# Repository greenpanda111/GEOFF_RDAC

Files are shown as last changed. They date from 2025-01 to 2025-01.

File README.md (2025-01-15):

# GEOFF
 3rd Year Engineering Module

 GEOFF is a 2 wheeled skid steered maze solving robot consisting of:
 2 motors with an ecoder each
 The encoders are wired to the ARB board using the expected pins as well as spare GPIO for the ultrasonics.
 
 4 IR sensors
 Two on the front for wall alignment using triganometry to calculate the angle to turn and for a wider field of view.
 One on either side of the robot for measuring the distance to the left and right of the robot.

 2 Ultrasonic sensors
 These are not currently utilised but my CAD design allows for them to be freely rotated so could be added for improved mapping capabilities in future.
 
 4 LED NeoPixel panels
 These form a 16x16 LED matrix to display live mapping of obstacles and route travelled along with current location and heading.
 The graphics library (All three NeoPixel libraries are created by Adafruit) used can allow for easy debugging. For example: writing the current angle onto the screen to test if it is being updated correctly as the robot turns.

 The Neopixel matrix can be controlled with one 5V signal pin. To achieve this, I had to design a level shifter to control it with the arduinos 3V3 signal

 2 Microswitches attached to the front corners of the robot to create a front bumper
 These prevent the robot from crashing into obstacles that the front IRs did not detect or catching on corners

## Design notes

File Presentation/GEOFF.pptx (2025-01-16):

## GEOFF

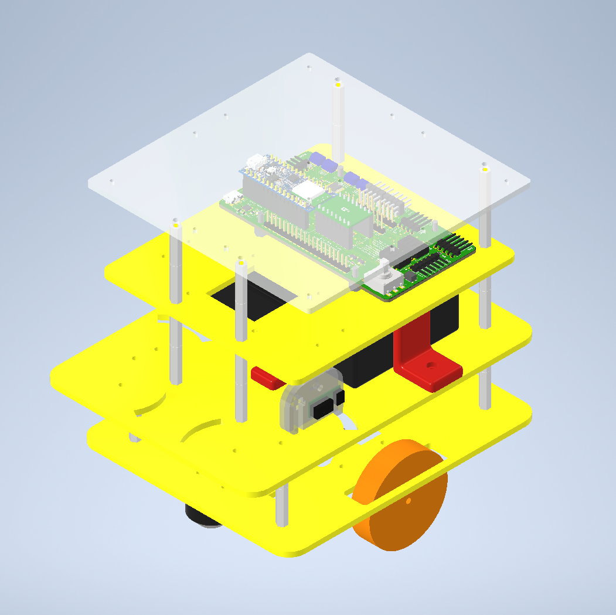
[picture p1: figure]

Ben Wiltshire

## LED Matrix

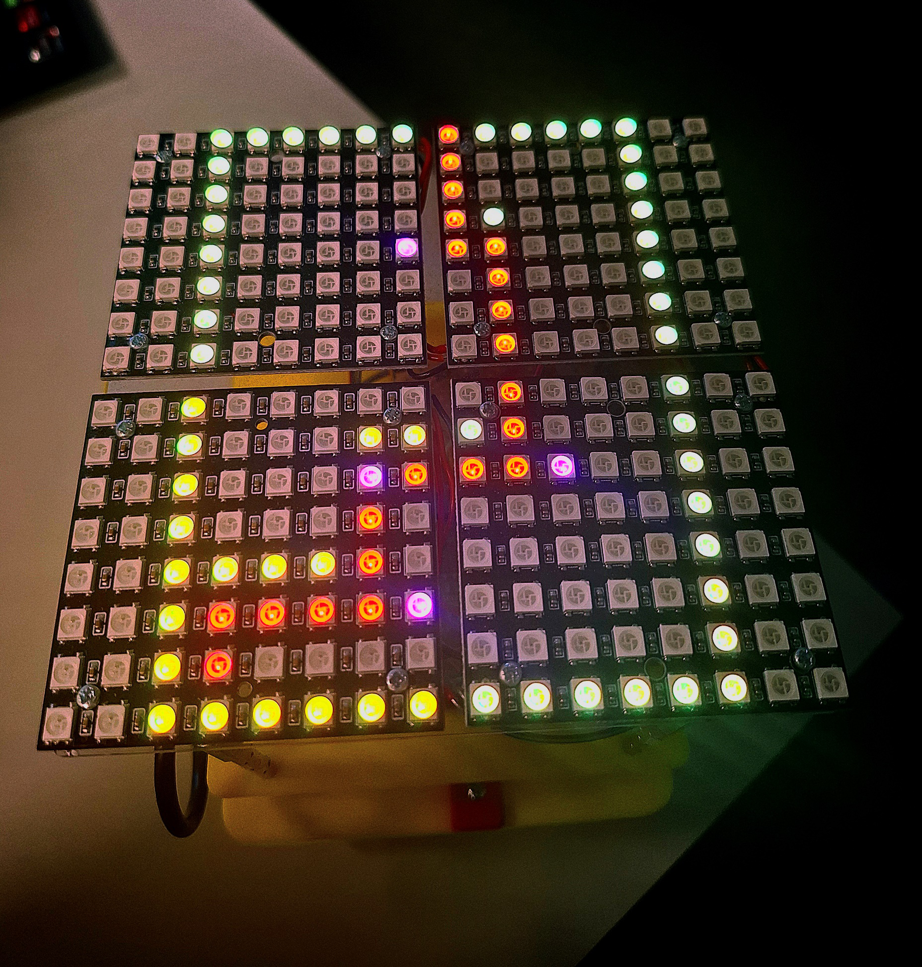
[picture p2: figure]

- 16x16 NeoPixel array
- Single pin programming
- Requires level shifter due to 5V signal
- Visualise maze solving in real time
Blue: Current Location
Red: Path Taken
Green: Obstacles
Purple: Direction

## Design

- 4 levels
- Minimum size is determined by the LED matrix
- Sensors on swivels
- Bottom IR not on swivel to keep wall aligning precise
- Cover over IR to prevent light interference
- Cable routing
- Optional slots for front ultrasonics

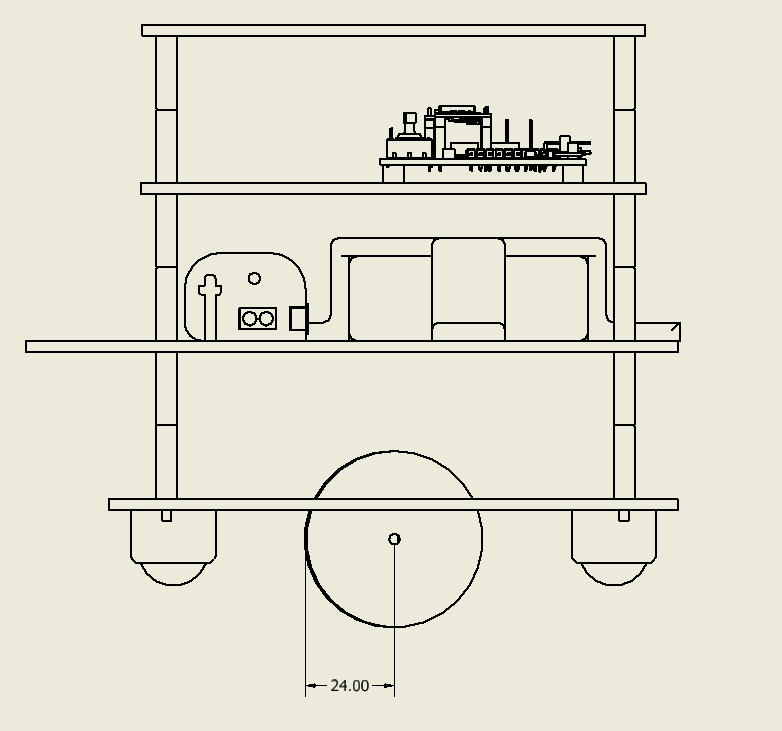
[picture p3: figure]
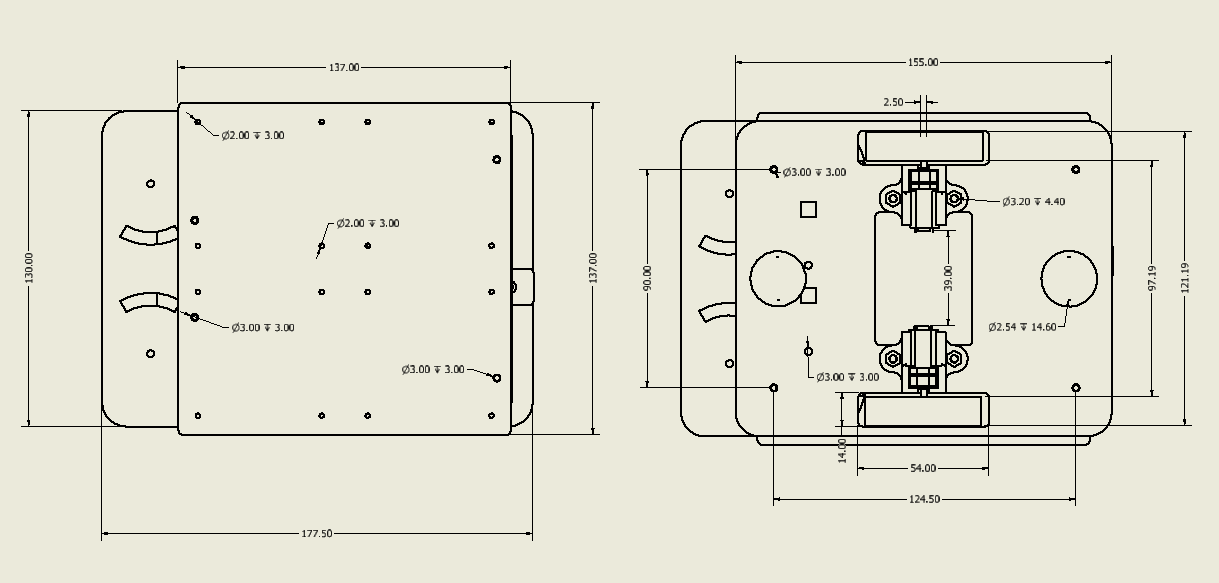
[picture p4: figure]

## Maze Solving

Turn to face the finish
Drive towards the finish until an obstacle is reached
Take measurements and take the best route around the obstacle
Shuffle along wall until it can move forward, towards the finish
If stuck in a dead end, navigate out

## Wall Aligning

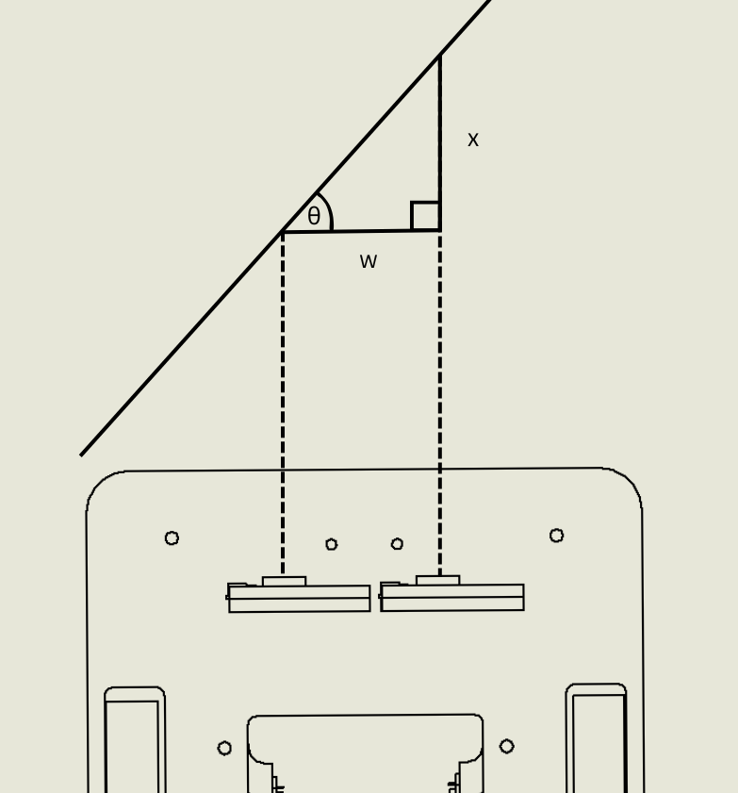
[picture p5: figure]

Trigonometry

## PCB

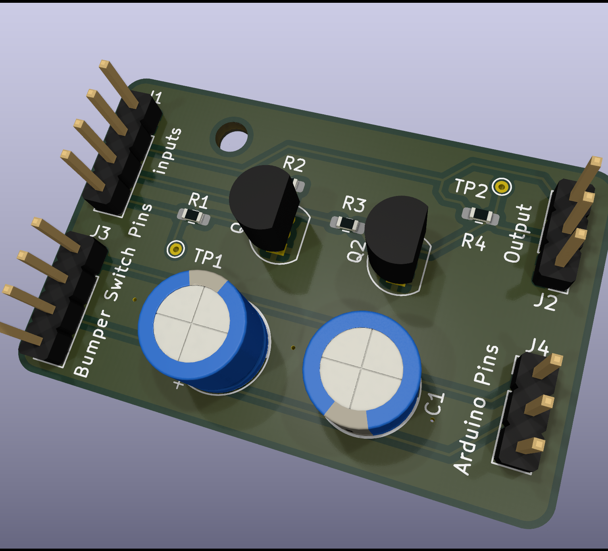
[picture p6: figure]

- LED Matrix Level Shifter
- Bumper Debouncing

## Next Steps…

Higher resolution occupancy grid
Calculating location of surrounding objects with side sensors after each move
Each bumper causing the robot to react differently

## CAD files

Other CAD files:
CAD/Final robot assembly Drawing.dwg
CAD/OldVersions/Final robot assembly Drawing.0003.dwg
CAD/0.75in Ball Caster (Pololu).ipt
CAD/Back.ipt
CAD/Battery 2023.ipt
CAD/Battery mount.ipt
CAD/Battery mount_MIR.ipt
CAD/Bottom layer.iam
CAD/Bottom layer2.ipt
CAD/Final robot assembly.iam
CAD/Front.ipt
CAD/IR Sensor Mount.iam
CAD/IR Sensor Mount.ipt
CAD/IR Sensor.ipt
CAD/M2.5 Hex Spacer 20mm 2023.ipt
CAD/M2.5 Hex Spacer 20mm.ipt
CAD/M2.5 Hex Spacer 5mm.ipt
CAD/Middle layer.iam
CAD/Middle layer.ipt
CAD/Motor assembly.iam
CAD/MotorHolder.ipt
CAD/NeoPixel Base.ipt
CAD/OldVersions/Bottom layer.0002.iam
CAD/OldVersions/Final robot assembly.0013.iam
CAD/OldVersions/Middle layer.0007.ipt
CAD/OldVersions/Middle layer.0008.iam
CAD/OldVersions/Top base 2.0002.ipt
CAD/OldVersions/Top layer.0003.iam
CAD/Pololu_MMG_Motor.ipt
CAD/Top base 2.ipt
CAD/Top layer.iam
CAD/wheel.ipt

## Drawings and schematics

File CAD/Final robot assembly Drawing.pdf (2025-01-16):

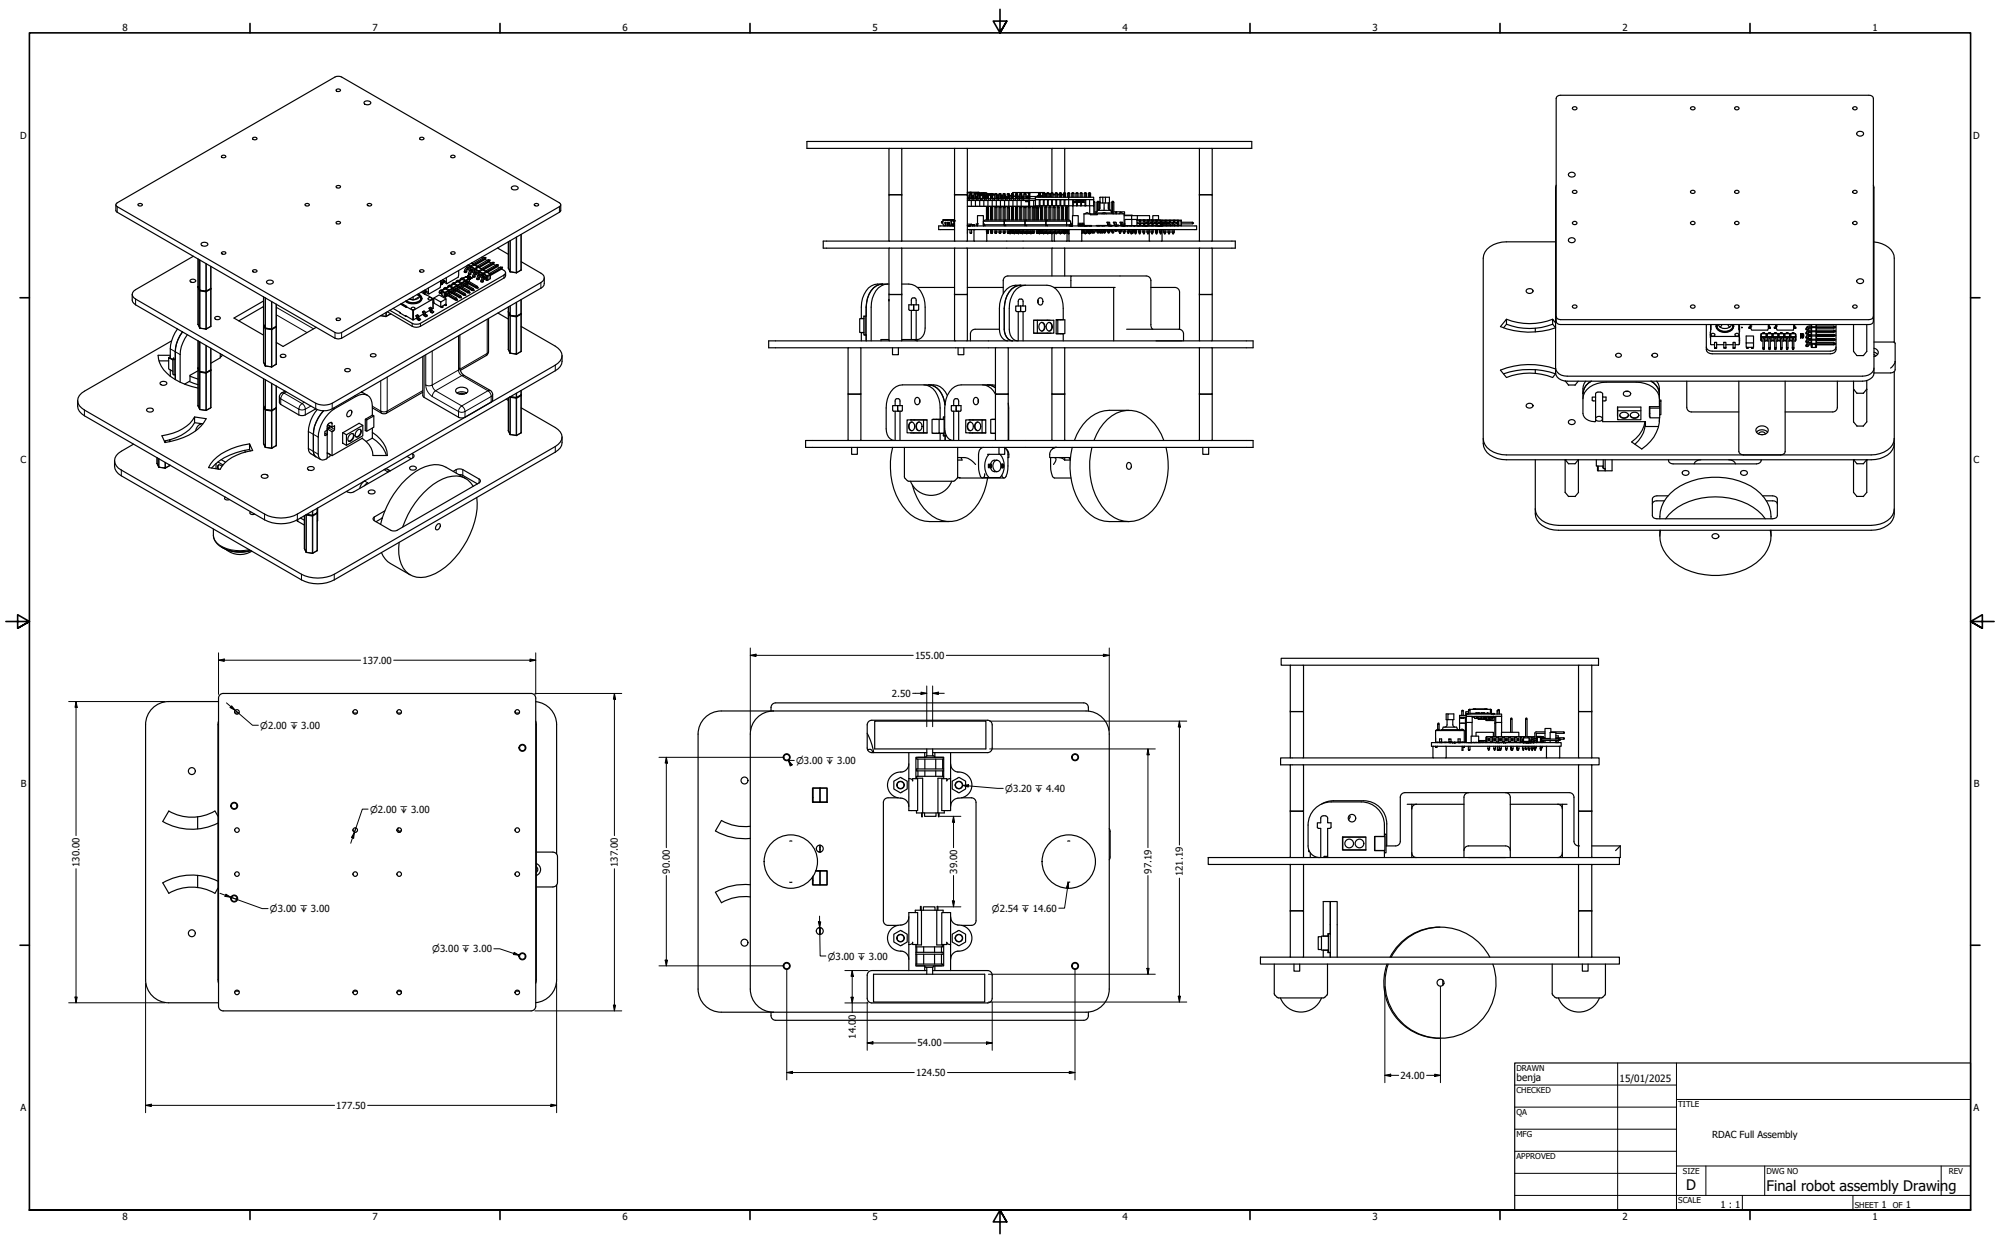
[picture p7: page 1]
SHEET 1 OF 1

RDAC Full Assembly

DWG NO
Final robot assembly Drawing

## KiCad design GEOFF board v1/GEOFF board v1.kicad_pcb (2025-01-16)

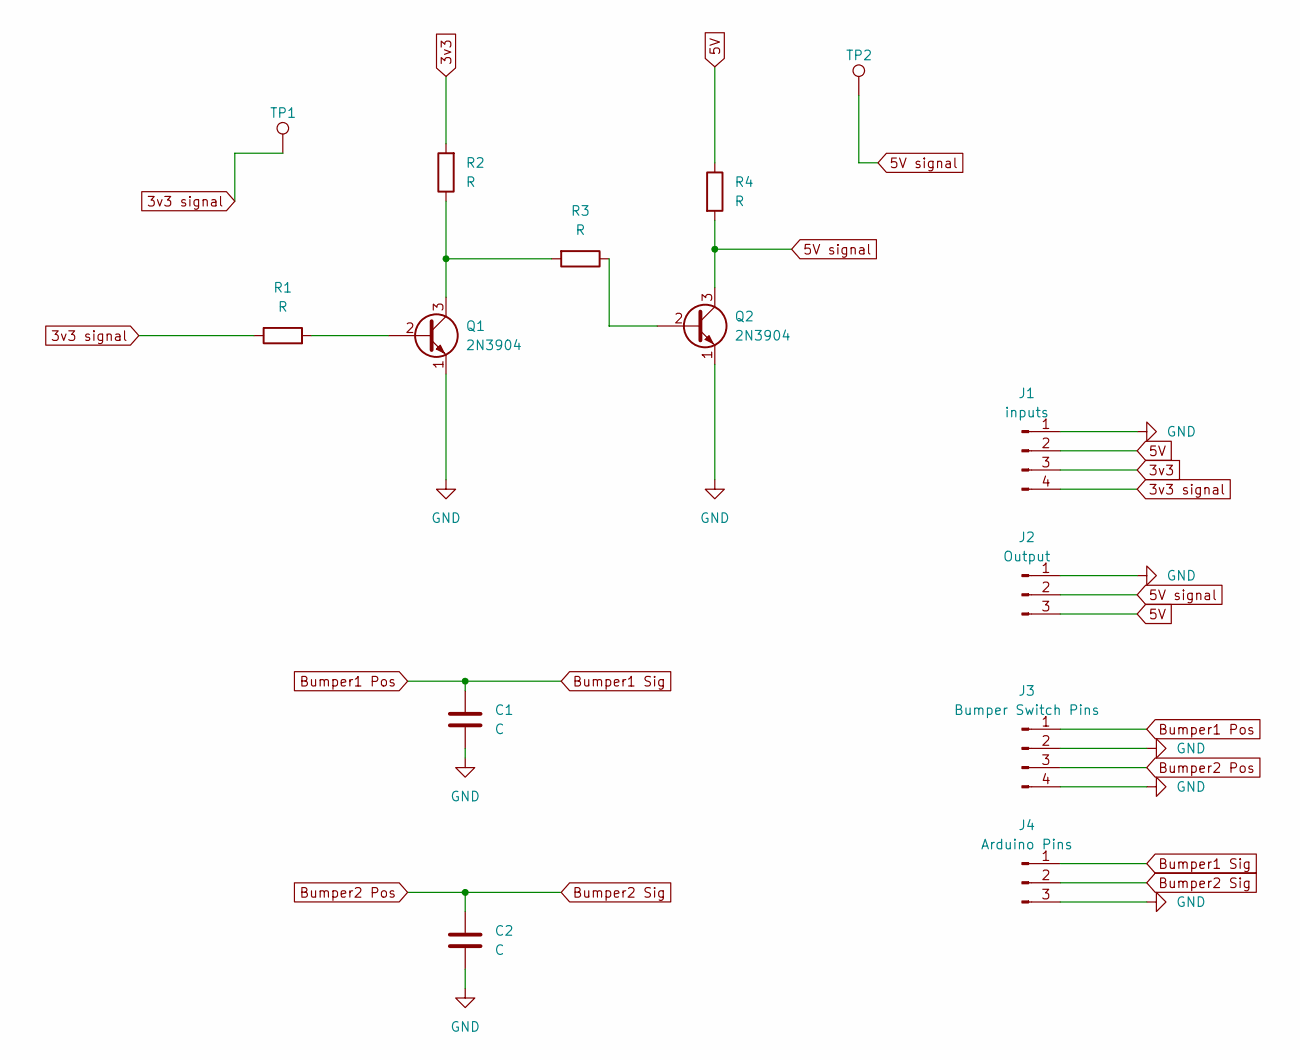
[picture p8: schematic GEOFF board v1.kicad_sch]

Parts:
C1, C2: C; CP_Radial_D7.5mm_P2.50mm
J1: inputs; PinHeader_1x04_P2.54mm_Vertical
J2: Output; PinHeader_1x03_P2.54mm_Vertical
J3: Bumper Switch Pins; PinHeader_1x04_P2.54mm_Vertical
J4: Arduino Pins; PinHeader_1x03_P2.54mm_Vertical
Q1, Q2: 2N3904; TO-92_Inline
R1, R2, R3, R4: R; R_0603_1608Metric_Pad0.98x0.95mm_HandSolder
TP1, TP2: TestPoint; TestPoint_THTPad_D1.0mm_Drill0.5mm

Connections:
3v3: J1.3, R2.2
3v3 signal: J1.4, R1.1, TP1.1
5V: J1.2, J2.3, R4.1
5V signal: J2.2, Q2.3 (C), R4.2, TP2.1
Bumper1 Pos: C1.1, J3.1, J4.1
Bumper2 Pos: C2.1, J3.3, J4.2
GND: C1.2, C2.2, J1.1, J2.1, J3.2, J3.4, J4.3, Q1.1 (E), Q2.1 (E)
unnamed: Q1.2 (B), R1.2
unnamed: Q1.3 (C), R2.1, R3.2
unnamed: Q2.2 (B), R3.1

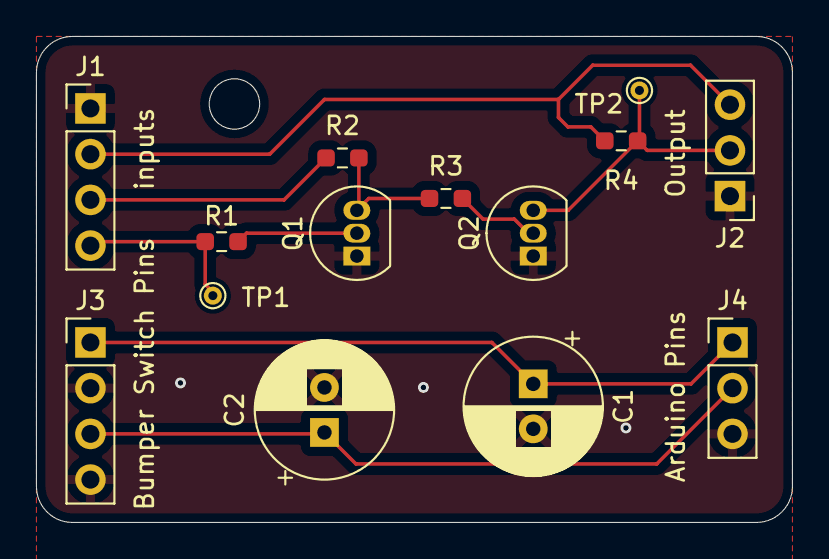
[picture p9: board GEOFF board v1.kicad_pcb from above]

Board: 2 copper layers, 42.0 x 27.0 mm, 14 parts (0 on the bottom side), 10 nets.

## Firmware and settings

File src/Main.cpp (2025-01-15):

#include "mbed.h"
#include "Motioncontroller.h"
#include "Map.h"
#include "MazeSolver.h"

using namespace mbed;

#define STD_DELAY 100000

void setup()
{
  // Set up the motor controller and motors
  motorControl.setup();
  // Initialise the LED map and occupancy grid
  mapSetup();
  // Reset robot position and set starting state
  mazeSolverSetup();
}

void loop()
{
  Serial.println("Loop Start --------------------------------");

  solveMaze();

  wait_us(STD_DELAY);

  Serial.println();
}

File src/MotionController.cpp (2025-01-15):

#include "Arduino.h"
#include "MotorClass.h"
#include "MotionController.h"
#include "mbed.h"
#include "Map.h"
#include "Bumpers.h"

using namespace mbed;

// proportional constant
#define KP 0.5
// default speed of the motors (%)
#define DEFAULTSPEED 0.4
// distance from the centre of the robot to the wheels
#define RADIUS 53
// motors are opposite so must turn in opposite directions for forward motion
#define LEFT_FORWARD 0.5
#define RIGHT_FORWARD -0.5

// build encoder objects for each motor
Encoder leftEncoder(LEFT_ENCODER_A, LEFT_ENCODER_B);
Encoder rightEncoder(RIGHT_ENCODER_A, RIGHT_ENCODER_B);

// build motors and pass in encoder objects
Motor leftMotor(LEFT_MOTOR_PWM, LEFT_MOTOR_DIRECTION, LEFT_FORWARD, leftEncoder);
Motor rightMotor(RIGHT_MOTOR_PWM, RIGHT_MOTOR_DIRECTION, RIGHT_FORWARD, rightEncoder);

// build motorController object with motors
MotionController motorControl(leftMotor, rightMotor);

// build bumpers
Bumper bumper(GPIO_PIN_3, GPIO_PIN_2);

MotionController::MotionController(Motor &leftMotor, Motor &rightMotor)
    : _leftMotor(leftMotor), _rightMotor(rightMotor)
{
}

void MotionController::setup()
{
  // run setup functions for motors and bumper
  _leftMotor.setup();
  _rightMotor.setup();
  bumper.setup();
  // set angle to face the finish
  _currentAngle = 0;
  // set alignment flag low
  _align = false;
}

int MotionController::getCurrentAngle()
{
  return _currentAngle;
}

void MotionController::setCurrentAngle(int angle)
{
  _currentAngle = angle;
}

void MotionController::setStuck(bool status)
{
  _stuck = status;
}

void MotionController::setAlign(bool status)
{
  _align = status;
}

void MotionController::forwardDist(int distance)
{
  // reset encoder counts to 0
  leftEncoder.reset();
  rightEncoder.reset();

  // while the robot has not moved the distance given and the bumpers have not been activated
  while ((abs(leftEncoder.getDistance()) < distance) & (abs(rightEncoder.getDistance()) < distance) & (_stuck == false))
  {
    // calculate error between encoders and multiply by proportional constant
    int error = (leftEncoder.getDistance() - rightEncoder.getDistance()) * KP;

    // alter the speed of each motor according to the error to keep the robot as straight as possible
    _leftMotor.move(DEFAULTSPEED + error);
    _rightMotor.move(-(DEFAULTSPEED - error));
  }

  // stop robot if distance is reached or obstacle hit
  stop();

  // if obstacle is hit
  if (_stuck == true)
  {
    // update location with the distance the encoders got to when collision occured
    mapUpdateLocation((leftEncoder.getDistance()+rightEncoder.getDistance())/2);
    // move away from the obstacle
    motorControl.avoid();
  }
  else
  {
    // update location with the distance travelled
    mapUpdateLocation(distance);
  }
}

void MotionController::reverseDist(int distance)
{
  // reset encoder counts to 0
  leftEncoder.reset();
  rightEncoder.reset();

  // while the robot has not moved the distance given
  while ((abs(leftEncoder.getDistance()) < distance) & (abs(rightEncoder.getDistance()) < distance))
  {
    // calculate error between encoders and multiply by proportional constant
    int error = (leftEncoder.getDistance() - rightEncoder.getDistance()) * KP;

    // alter the speed of each motor according to the error to keep the robot as straight as possible
    _leftMotor.move(-(DEFAULTSPEED - error));
    _rightMotor.move((DEFAULTSPEED + error));
  }

  // stop robot if distance is reached
  stop();
  mapUpdateLocation(-distance);
  
}

void MotionController::rotate(int angle)
{
  // reset encoder counts to 0
  leftEncoder.reset();
  rightEncoder.reset();
  // increase the robots angle by the given angle
  updateCurrentAngle(angle);

  // calculate distance for the motors to turn for rotation of the robot to reach the given angle
  float distance = arcLength(abs(angle));

  // if rotating counter clockwise
  if (angle < 0)
  {
    // while the motors have not turned the distance given
    while ((abs(leftMotor.getEncoderDist()) < distance) & (abs(rightMotor.getEncoderDist()) < distance))
    {
      // calculate error and multiply by proportional constant
      int error = (leftEncoder.getDistance() + rightEncoder.getDistance()) * KP;

      // alter the speed of each motor to keep them turning at the same rate
      _leftMotor.move((DEFAULTSPEED - error));
      _rightMotor.move((DEFAULTSPEED + error));
    }
  }
  // if rotating clockwise
  else
  {
    // while the motors have not turned the distance given
    while ((abs(leftMotor.getEncoderDist()) < distance) & (abs(rightMotor.getEncoderDist()) < distance))
    {
      // calculate error and multiply by proportional constant
      int error = (leftEncoder.getDistance() + rightEncoder.getDistance()) * KP;

      // alter the speed of each motor to keep them turning at the same rate
      _leftMotor.move(-(DEFAULTSPEED + error));
      _rightMotor.move(-(DEFAULTSPEED - error));
    }
  }

  // stop robot if distance to turn by is reached
  stop();
}

float MotionController::arcLength(float angle)
{
  // calculate arc length using equation
  // convert angle to radians
  float arcLength = (2 * PI * RADIUS * (angle / 360));
  return arcLength;
}

void MotionController::updateCurrentAngle(int angleChange)
{
  // if rotate function is called by the wall alignment function, don't change the angle stored
  if (_align == false)
  {
    // add the change in angle to the current angle
    _currentAngle += angleChange;

    // if the result is larger than 360
    if (_currentAngle >= 360)
    {
      // loop back round to zero and continue adding from there
      _currentAngle = _currentAngle - 360;
    }
    // if the result goes negative
    else if (_currentAngle < 0)
    {
      // loop back to 360 and continute subtracting from there
      _currentAngle = 360 - abs(_currentAngle);
    }
  }
  else
  {
  }
}

void MotionController::avoid(void)
{
  // reset stuck flag
  motorControl.setStuck(false);
  // stop motors from spinning
  motorControl.stop();
  // save the location of the obstacle in front
  drawObstacle();
  // reverse away from the obstacle
  motorControl.reverseDist(100);
}

void MotionController::stop()
{
  _leftMotor.stop();
  _rightMotor.stop();
}

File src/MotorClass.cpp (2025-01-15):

#include "MotorClass.h"
#include "Encoders.h"

#include "mbed.h"
using namespace mbed;

#define VELOCITY_TICKER_PERIOD 0.1

Motor::Motor(PinName PwmPin, PinName dirPin, bool forwardDirection, Encoder &encoder)
    : _PwmPin(PwmPin), _dirPin(dirPin), _forwardDirection(forwardDirection), _encoder(encoder) {}

void Motor::setup(void)
{
  _PwmPin.period(PWM_PERIOD);
  // Set motor power to 0 so they start off by default
  _PwmPin.write(0.0f);
  // Calculate velocity every ticker period
  _velocityTicker.attach(callback(this, &Motor::calculateCurrentVelocity), VELOCITY_TICKER_PERIOD);
}

void Motor::move(float power)
{
  // If power given is positive
  if (power > 0)
  {
    // Change motor direction so that it drives forward relative to the robot
    _dirPin.write(_forwardDirection);
  }
  else
  {
    // Reverse motor direction
    _dirPin.write(!_forwardDirection);
  }
  // Rotate the motor at the given power
  _PwmPin.write(abs(power));
}

void Motor::stop(void)
{
  _PwmPin.write(0.0f);
}

void Motor::calculateCurrentVelocity(void)
{
  // Velocity in mm/s
  // Change in distance over known time
  _currentVelocity = (abs(_encoder.getDistance()) - _lastEncoderDist) / VELOCITY_TICKER_PERIOD;
  _lastEncoderDist = abs(_encoder.getDistance());
}

float Motor::getEncoderDist(void)
{
  return _encoder.getDistance();
}

float Motor::getEncoderCount(void)
{
  return _encoder.getCount();
}

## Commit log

2024-11-15 LED Bitmaps
2024-11-15 Shitty encoder code
2024-11-18 Refactored Encoders
2024-11-19 Encoders in Controller
2024-11-20 PID beginnings
2024-11-28 PID functional
2024-12-06 PID to be calibrated
2024-12-13 PID calibration
2025-01-08 Count reset to float
    [Encoders.cpp, Main.cpp, MotorClass.cpp]
2025-01-15 CAD Included
    [0.75in Ball Caster (Pololu).ipt, Battery mount_MIR.ipt, Bottom layer2.ipt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]
2025-01-15 CAD and PPT
    [Back.ipt, Battery 2023.ipt, Battery mount.ipt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]
2025-01-16 Assembly Fixed. Presentation Finished. PCB added
    [Bottom layer.0002.iam, Bottom layer.iam, Final robot assembly Drawing.0002.dwg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]
